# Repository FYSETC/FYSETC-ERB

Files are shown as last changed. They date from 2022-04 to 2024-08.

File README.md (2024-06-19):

# Introduction
ERB is a 3D printer multi-color control board based on RP2040, mainly used in Enraged Rabbit project. It can also be used in other two-axis stepper motor control situations.

# Update:
## [V1](./V1.0):
- MCU RP2040 
- 28V Input Max，5V@3A
- USB interface
- 2 x TMC2209 Onboard
- 5V RGB，Servo supported
- Extra pins are brought out to pin headers.

## [V2](./V2.0):
- Add CANBUS interface 
- Add 20*30 heat sinks 
- Replace with a 4Pin connector, which can be quickly plugged in and out, for Power & USB/CAN.
- Add optional USB and CANBUS interfaces 
- Add status indicator for Katapult bootloader or status indication.
- Preset thermistor temperature measurement circuit
- 12 x IO for gate sensors/switch
- Onboard integrated heat sink

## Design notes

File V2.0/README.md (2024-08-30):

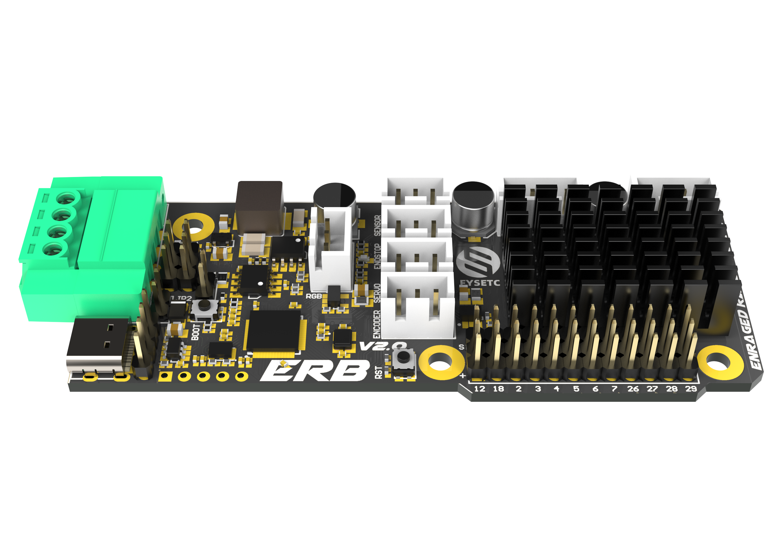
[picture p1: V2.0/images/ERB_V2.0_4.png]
erb


# Introduction

ERB V2 is a 3D printer multi-color control board based on RP2040, mainly used in Enraged Rabbit project. Based on V1, CANBUS connection is added, and the terminal connection method and layout are readjusted to better meet the needs of Enraged Rabbit V2.

## Features

- MCU RP2040 
- 28V Input Max，5V@3A
- USB & CANBUS interface
- 2 x TMC2209 Onboard
- 12 x IO for gate sensors/switch
- Onboard integrated heat sink
- 5V RGB，Servo supported
- Power supply/CAN integrated interface for easy connection

## Hardware

There are schemetic, silk and dwg file in `Hardware` folder.

### Pinout
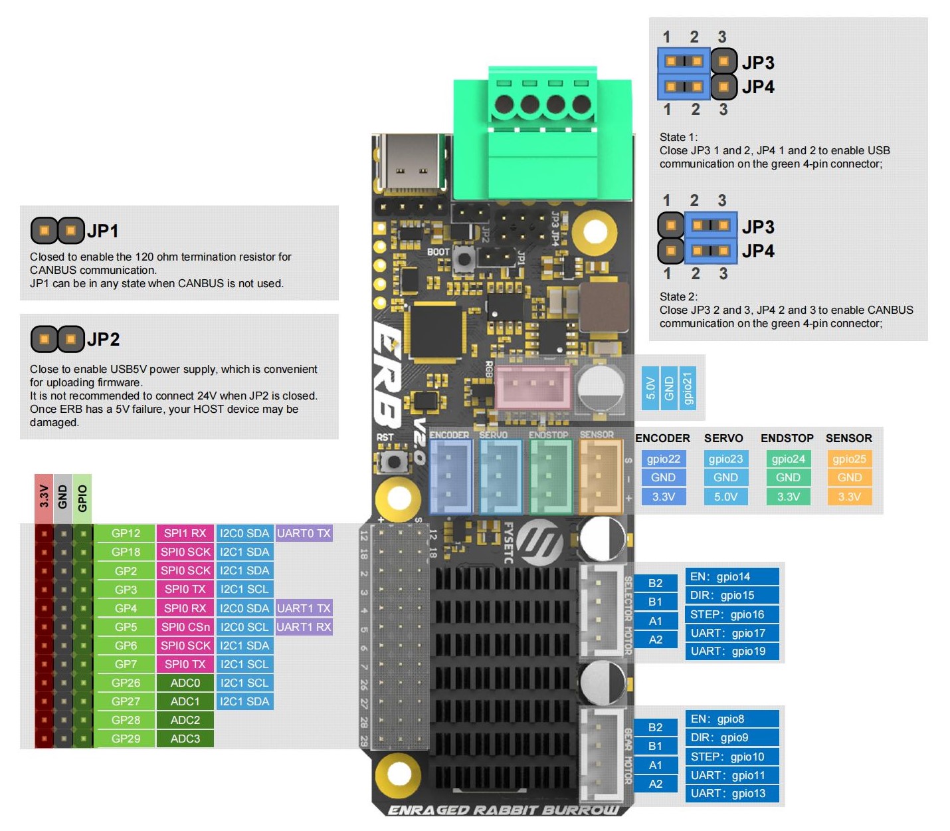
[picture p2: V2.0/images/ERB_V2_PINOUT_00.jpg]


## Firmware

### Compile and upload
In order to compile and upload at one time, you need to follow the steps below to put RP2040 into dfu mode.

1. Step 1: Connect 24V (Power on the board)
2. Step 2: Connect USB-C cable to your Klipper device (usually Raspberry Pi)
3. Step 3: Push and hold the BOOTSEL button
4. Step 4: Push the RST button and hold 0.5 seconds
5. Step 5: Release the RST button, after 3 seconds, Release the bootsel button
6. Verify your device is in boot mode connected by running the following command:

```shell
lsusb
```

The output should contain an entry looking like 2e8a:0003 Raspberry Pi RP2 Boot


On your klipper device (usually Raspberry Pi) run the following to create your make configuration:

```shell
cd  ~/klipper
make clean
make menuconfig
```

Select the following menuconfig settings

Use USB communication

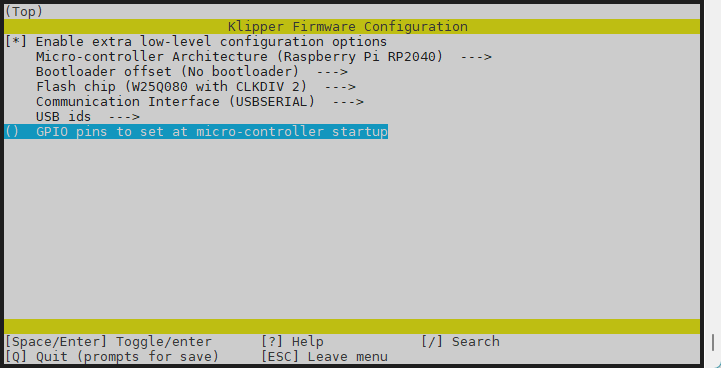
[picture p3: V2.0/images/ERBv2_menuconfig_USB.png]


Use CANBUS communication

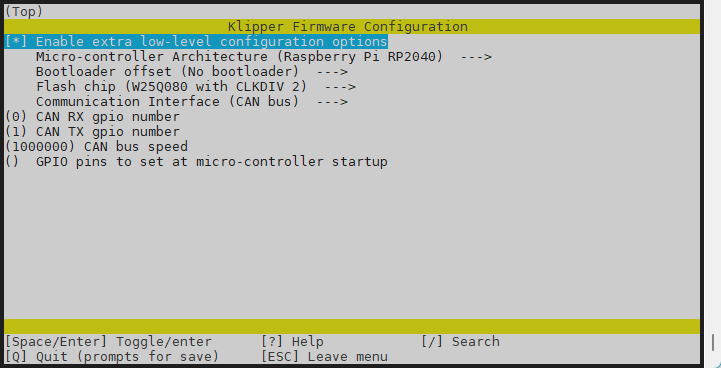
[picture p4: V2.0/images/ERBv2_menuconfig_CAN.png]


And create and upload the firmware files by running the following:

```shell
make flash FLASH_DEVICE=2e8a:0003
```
The output looks like the following - IF you are prompted (you might or might not) for a password, enter the password of your current user account.


Now restart your fystec-erb by disconnecting 24V - waiting some seconds and reconnecting 24V again.
Or press the reset button for one second and then release it.
You should be able to see it as usual klipper device within 
```shell
ls /dev/serial/by-id
```
### Configuration

See `ercf_hardware.cfg` in this repository `config` folder.

---------------------------------------------------

> [!TIP]
> We recommend using the katakulpt bootloader, whether you use USB or CANBUS communication. This can avoid many strange problems.
> 
> Configuration of the katakulpt bootloader:
> 
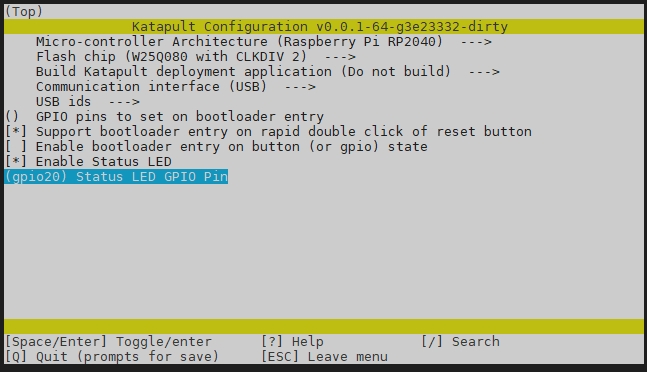
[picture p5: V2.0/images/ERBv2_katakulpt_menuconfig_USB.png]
ERBv2_katakulpt_menuconfig_USB
> 
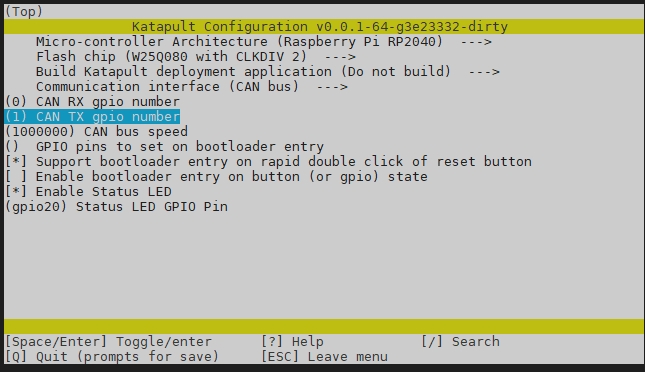
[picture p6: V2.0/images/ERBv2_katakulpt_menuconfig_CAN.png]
ERBv2_katakulpt_menuconfig_CAN
> 
> 
> Configuration of klipper using katakulpt:
> 
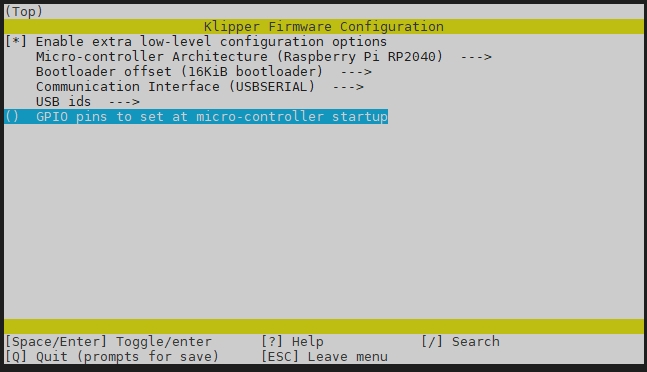
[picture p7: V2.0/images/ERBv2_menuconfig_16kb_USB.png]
ERBv2_menuconfig_16kb_USB
> 
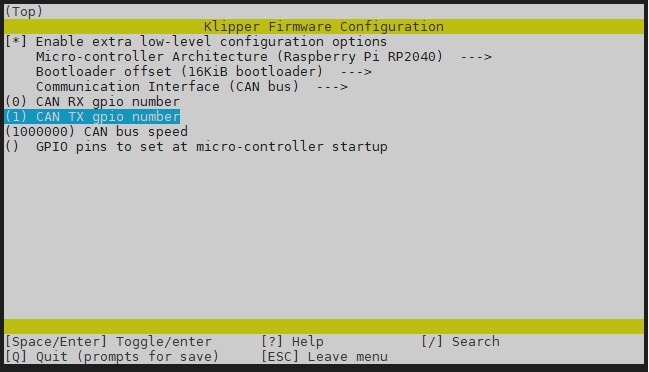
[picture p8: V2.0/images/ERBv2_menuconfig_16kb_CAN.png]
ERBv2_menuconfig_16kb_CAN
>

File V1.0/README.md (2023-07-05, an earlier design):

# FYSETC-ERB

This is dedicated controller board for VORON ERCF

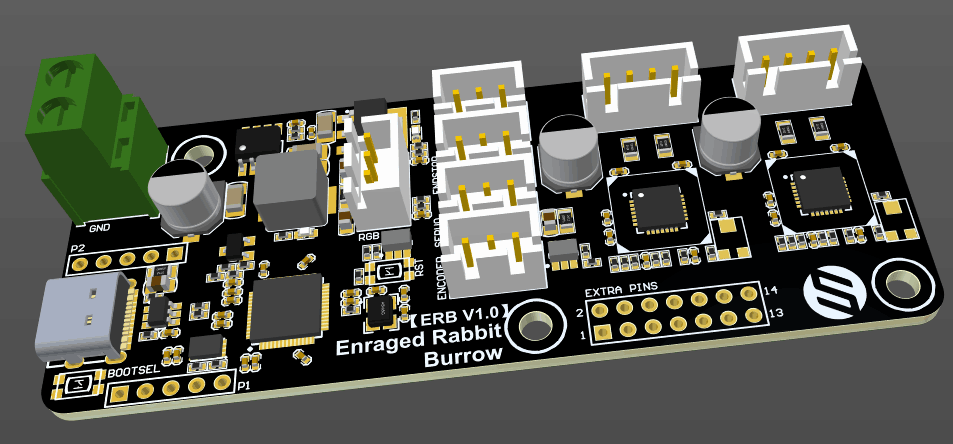
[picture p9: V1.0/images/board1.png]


## Features

1. Base on popular RP2040 chip, cheep,available

2. Power management chip, comparing to LDO chip, less heat, more powerful, more steady

3. USB type-C interface and more extra pins out.

## Hardware

There are schemetic, silk and dwg file in `Hardware` folder.

## Firmware

### Compile options
On your klipper device (usually Raspberry Pi) run the following to create your make configuration:

```shell
cd  ~/klipper
make clean
make menuconfig
```

Select the following menuconfig settings

makemenuconfig

And create the firmware files by running the following:

```shell
make
```

### Firmware upload

#### 1.With your windows PC

Step 1: Connect 24V (Power on the board)

Step 2: Connect USB-C cable to your Klipper device (usually Raspberry Pi)

Step 3: Push and hold the BOOTSEL button

Step 4: Push the RST button and hold 0.5 seconds

Step 5: Release the RST button, after 3 seconds, Release the bootsel button

Step 6: `RPI-RP2` folder will show up on your computer, copy your built firmware `klipper.uf2` to the folder.

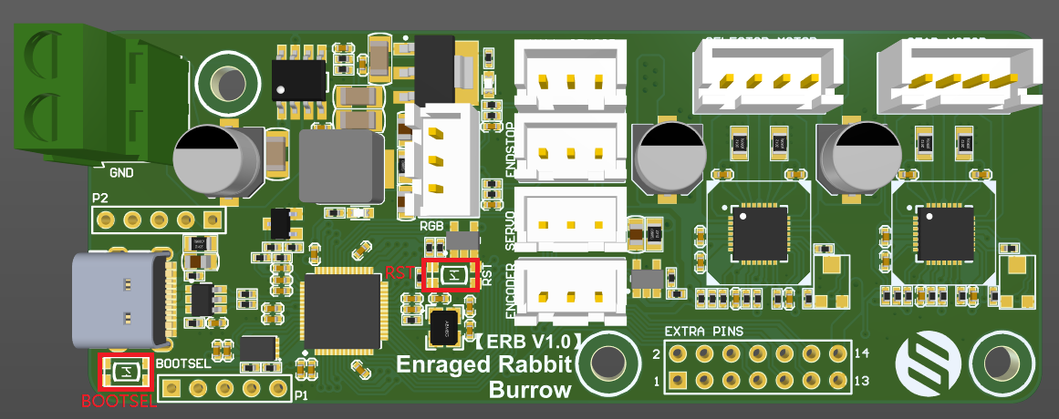
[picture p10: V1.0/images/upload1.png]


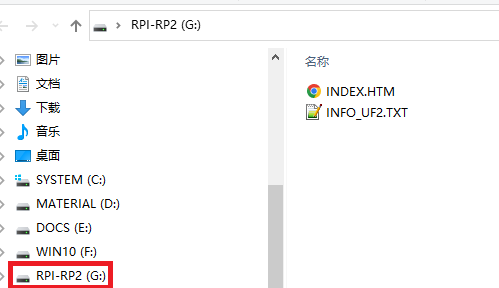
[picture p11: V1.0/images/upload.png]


#### 2. With your Pi 

Thanks for mk-maddin's work:
https://github.com/FYSETC/FYSETC-ERB/issues/2#issuecomment-1618902635

##### Connecting the board and bring it into flash mode

Step 1: Connect 24V (Power on the board)

Step 2: Connect USB-C cable to your Klipper device (usually Raspberry Pi)

Step 3: Push and hold the BOOTSEL button

Step 4: Push the RST button and hold 0.5 seconds

Step 5: Release the RST button, after 3 seconds, Release the bootsel button

Verify your device is in boot mode connected by running the following command:

```shell
lsusb
```

The output should contain an entry looking like 2e8a:0003 Raspberry Pi RP2 Boot


##### Flashing the firmware
Now we do not flash the fimware by directly copying it to the storage, but we flash it using the following command:

```shell
make flash FLASH_DEVICE=2e8a:0003
```

The output looks like the following - IF you are prompted (you might or might not) for a password, enter the password of your current user account.


Now restart your fystec-erb by disconnecting 24V - waiting some seconds and reconnecting 24V again.
You should be able to see it as usual klipper device within 
```shell
ls /dev/serial/by-id
```

### Configuration

See `ercf_hardware.cfg` in this repository `config` folder.

### Known issues

The mark of GPIO24 and GPIO25 is swapped, check the silk file [here](https://github.com/FYSETC/FYSETC-ERB/blob/main/hardware/Silk%20Fixed.pdf).

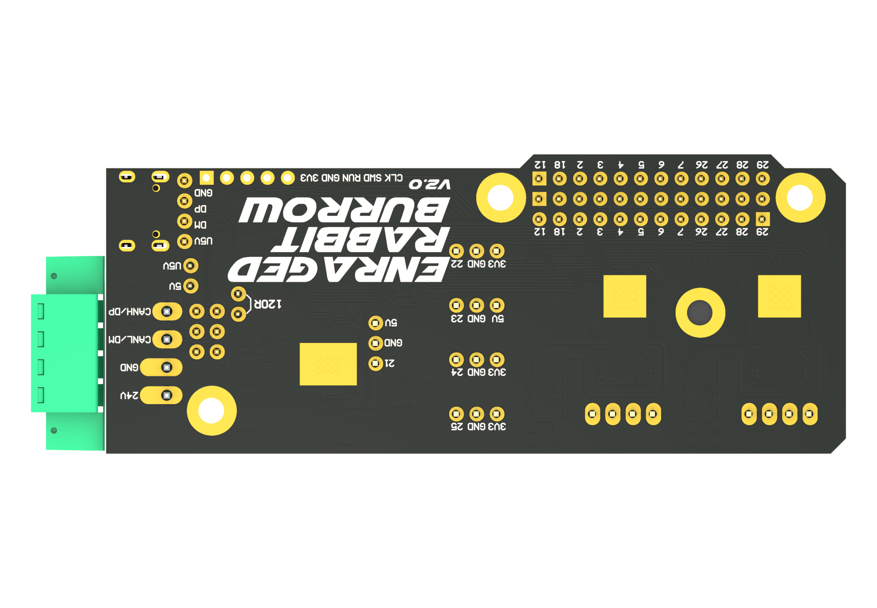
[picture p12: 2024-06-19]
V2.0/images/ERB_V2.0_2.png

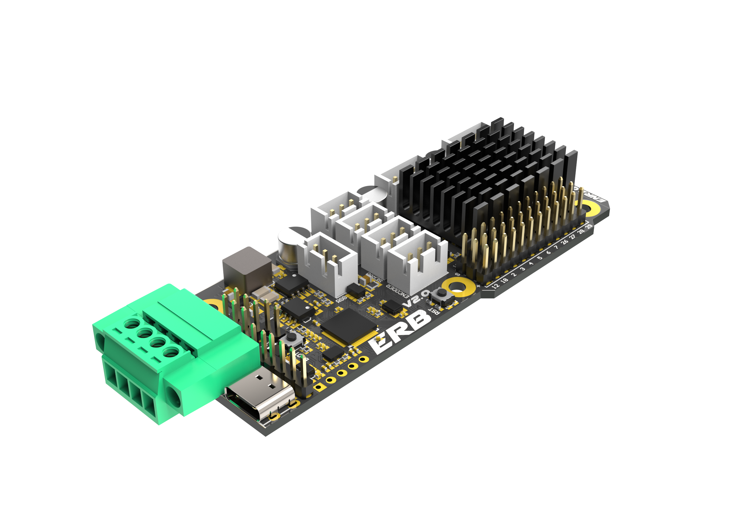
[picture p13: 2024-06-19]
V2.0/images/ERB_V2.0_3.png

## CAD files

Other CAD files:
V2.0/CAD/ERB V2.0.DWG

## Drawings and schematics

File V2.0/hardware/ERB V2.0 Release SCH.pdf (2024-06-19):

## Raspberry Pi

# GPIO4 6 GND 57

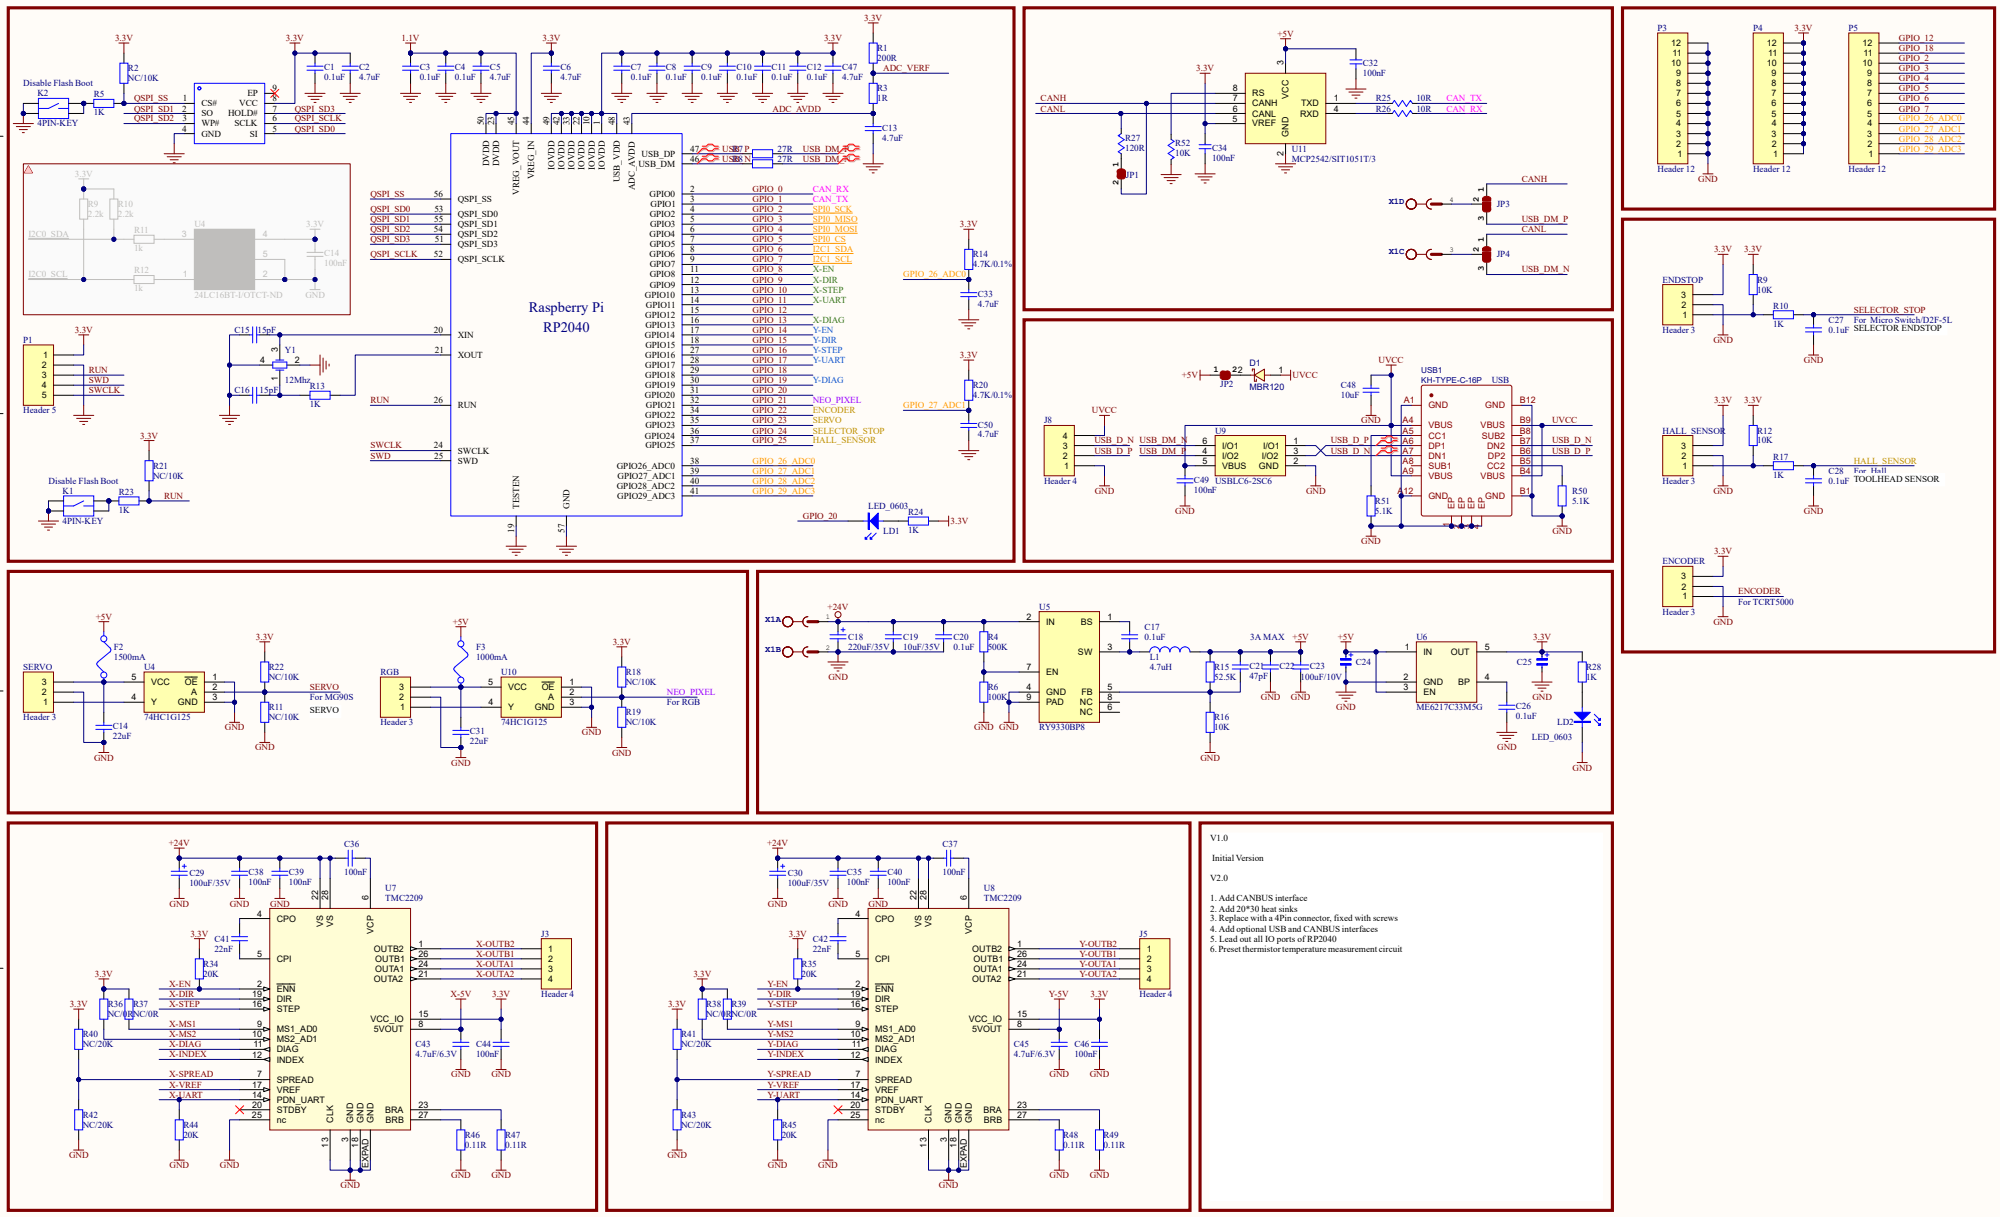
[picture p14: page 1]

1. Add CANBUS interface
2. Add 20*30 heat sinks
3. Replace with a 4Pin connector, fixed with screws
4. Add optional USB and CANBUS interfaces
5. Lead out all IO ports of RP2040
6. Preset thermistor temperature measurement circuit

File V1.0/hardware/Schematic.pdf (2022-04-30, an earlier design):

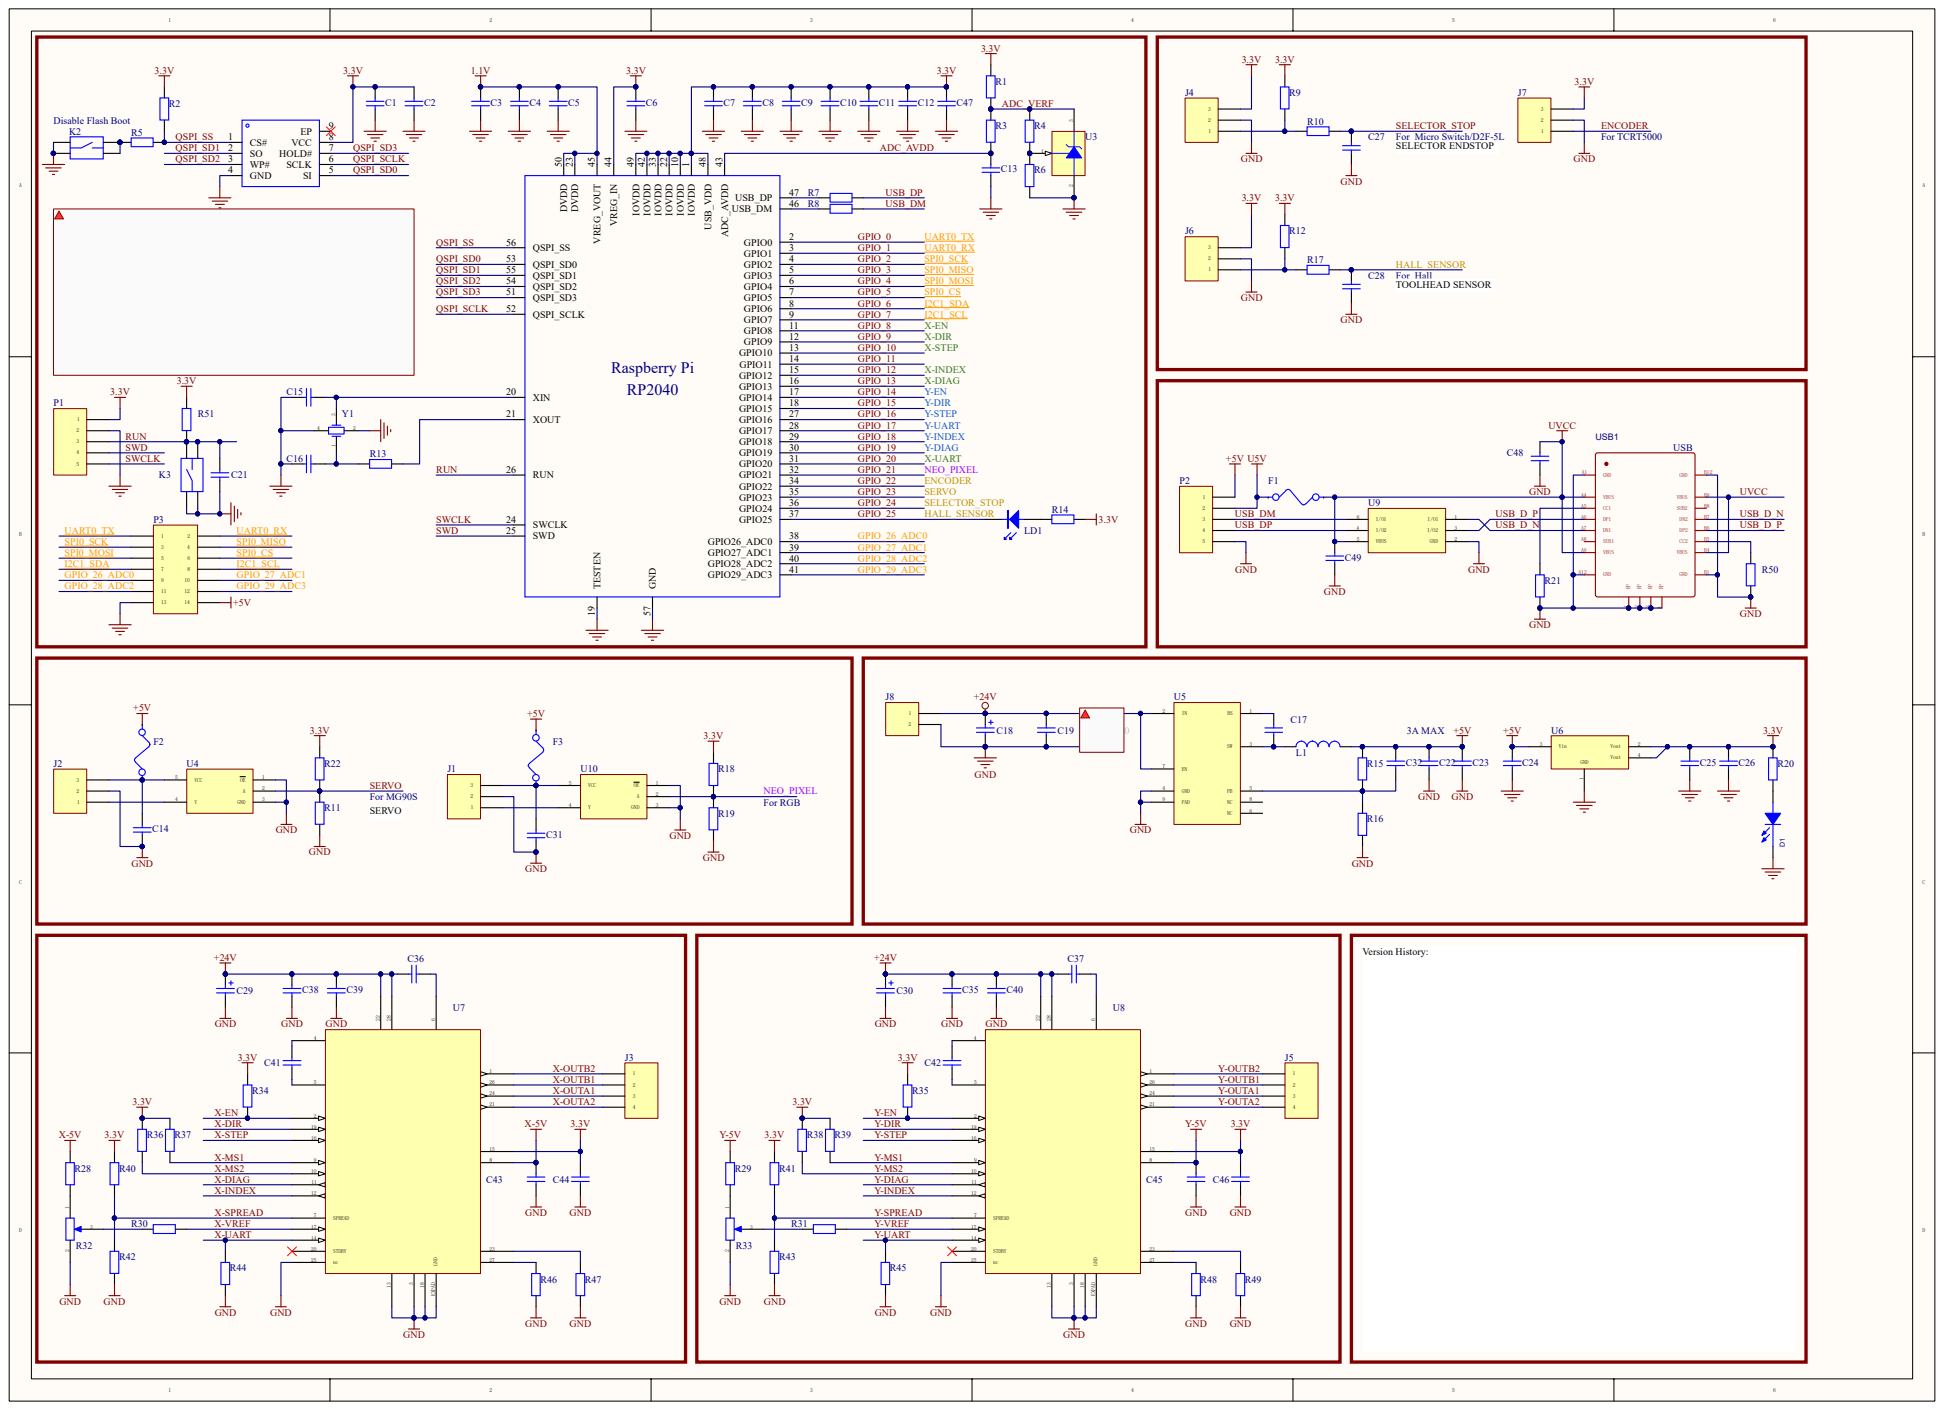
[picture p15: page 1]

XIN 20 | GPIO_7 I2C1_SCL GPIO_8 X-EN X-DIR X-STEP X-INDEX X-DIAG Y-EN Y-DIR Y-STEP Y-UART Y-INDEX Y-DIAG X-UART NEO_PIXEL ENCODER SERVO SELECTOR_STOP | GND

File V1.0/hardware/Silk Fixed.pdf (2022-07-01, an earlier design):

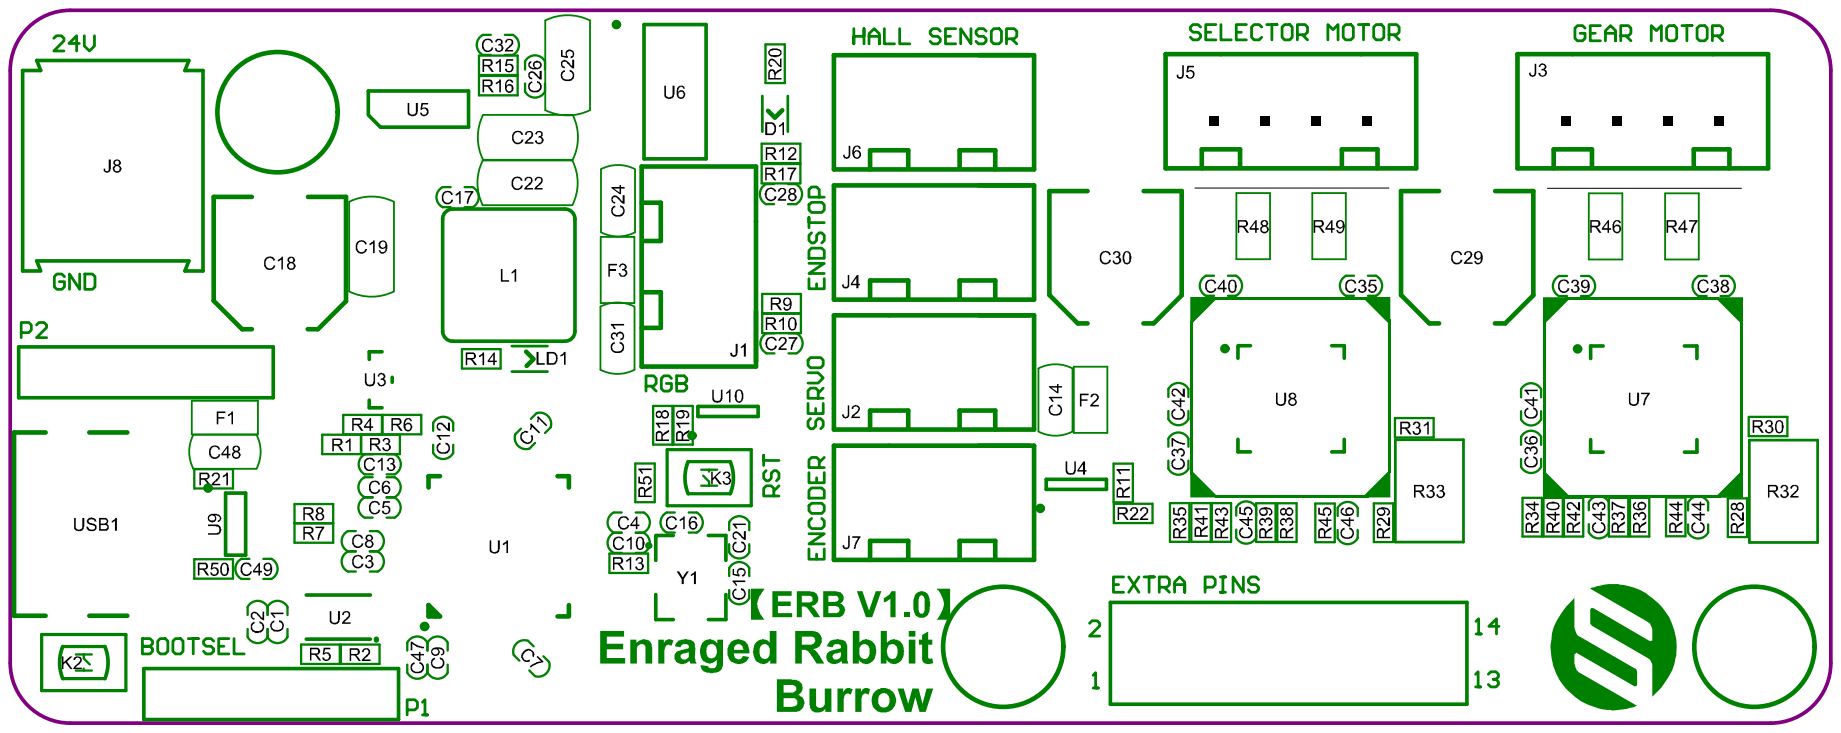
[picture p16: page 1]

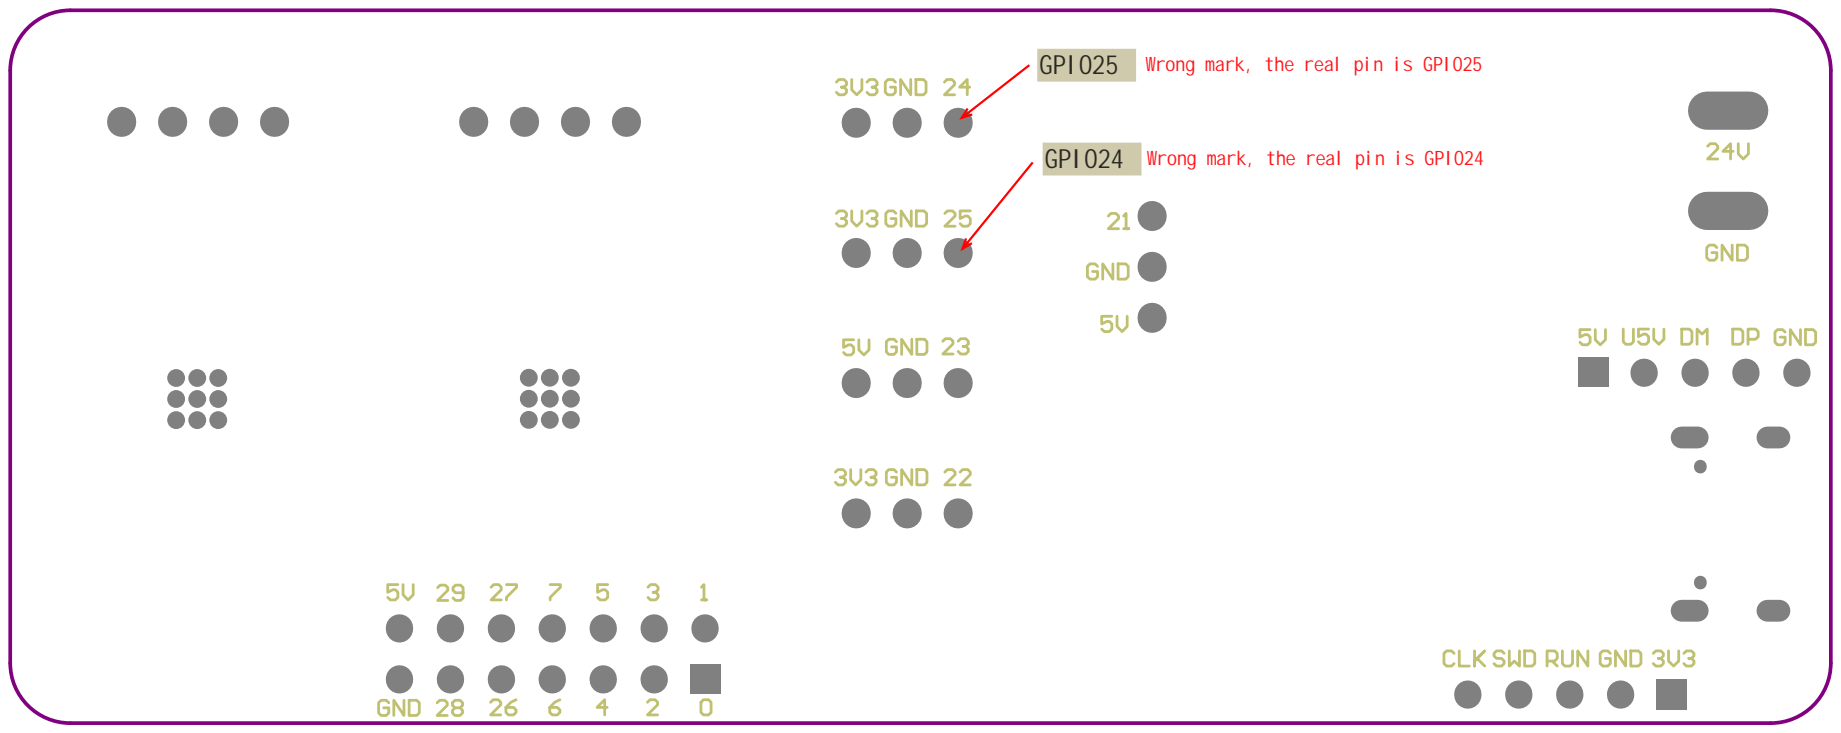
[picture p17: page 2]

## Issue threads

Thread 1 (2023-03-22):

Erb V1.1 make menuconfig

reneprettentaler, 2023-03-22:
Make menuconfig is not the same as in the reader.
What should I config in the menuconfig for flashing.
board does phenyl connct to Klipper with pressing the reset button.

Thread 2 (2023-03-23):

RP2040 MCU does not connect until reset is pressed

JoaquinBerrios, 2023-03-23:
The ERB board fails to connect to the host at boot until the reset button is pressed and the klipper service is re-started. This appears to be the same issue mentioned in the BTT SKR-Pico issue named here: https://github.com/bigtreetech/SKR-Pico/issues/2

I was able to implement a similar workaround as that mentioned in the thread and described in more detail here:
https://github.com/Drachenkaetzchen/VoronMisc/blob/main/SKR-Pico-Reset.md
by connecting pin 3 in P1 to a GPIO pin on my the host raspberry pi and resetting the ERB at boot time before the klipper service starts, but would prefer an actual fix that would allow me to undo that hack.

matthewj301, 2023-03-25:
yup also having this issue, although intermitently

JoaquinBerrios, 2023-05-03:
Looks like this was addressed in a commit last week in Klipper. I built firmware for a couple of RP2040 boards using the fixed usbserial.c from this commit and they connect via USB with no issues so far. Just thought I would share for other having this issue to try and see if this resolves it for them.
https://github.com/Klipper3d/klipper/commit/bec1d957d216986da8da216aca557c4d31623fd2

PatrikTheDev, 2023-05-20:
I’m running the latest Klipper version (both ERB and Pi) and I’m still having issues, though mine doesn’t connect after a reset, it often needs MUCH more convincing. I already requested a partial refund but is there a way to save the board? That Klipper commit didn’t work for me since I’m running it already

mk-maddin, 2023-06-16:
@PatrikTheDev
I was able to resolve this issue by flashing with the following options - Klipper v0.11.0-221-g6ce2bd61

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

PatrikTheDev, 2023-06-16:
IIRC that’s what I flashed with before but it didn’t work. I got it working with the CanBoot workaround though. As it turns out the board still wasn’t quite healthy and I got a partial refund from Fysetc

mk-maddin, 2023-06-16:
ok...maybe I was a bit too fast - I am now running into "Timeout on wait for 'tmcuart_response' response" error on like every seconds stepper_buzz command
Re-flashing with the default chip "W25Q080 with CLKDIV 2" solves the stepper_buzz error, but again causes disconnect at every restart

PatrikTheDev, 2023-06-16:
Have you tried flashing CanBoot to it yet? Seems to also work for the SKR Pico

mk-maddin, 2023-06-17:
No not yet ...
I am not using CanBus at all at the moment and after reading through the CanBoot guideline, to be truth I have no idea how to "2. Build klipper wiht CAN support" ( https://github.com/Arksine/CanBoot#uploading-klipper )

PatrikTheDev, 2023-06-17:
I’m not using CAN either right now, CanBoot offers a USB mode. Look into the SKR Pico repo, issue number 2 for more information

mk-maddin, 2023-06-17:
To be truth I am not 100% sure if I really see the same issue as the skr pico people describe ...
My device does not show at all within /dev/serial/* or /dev/tty* after every RST or power disconnect of 24V,
until I re-flash a .uf2 via the "storage" (pressing "bootsel"+"rst")  mode.
I can press "rst" during boot or run the [GPIO workaround](https://github.com/Drachenkaetzchen/VoronMisc/blob/main/SKR-Pico-Reset.md) - all without any success unti I re-flash and keep the device online.

So klipper not able being to connect is only a "victim" of the ERB not correctly booting into the flashed firmware / serial mode after power off / reset.
This happens as I just tested for klipper.uf2 as for canboot.uf2

jeanres, 2023-06-28:
Same issue here.

mk-maddin, 2023-07-03:
I think I was able to solve the issue for me now by using the same flash procedure as done with the 3D Mellow Fly ERCF Easy BRD board ( https://mellow.klipper.cn/#/board/fly_ercf/flash ) - as most of this is chinese and I had to translate via online translator service - here is what I did:

### **1. Prepare Firmware**
On your klipper device (usually Raspberry Pi) run the following to create your make configuration:
`cd  ~/klipper`
`make clean`
`make menuconfig`

Select the following menuconfig settings
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
And create the firmware files by running the following:
`make`

### **2. Connecting the board and bring it into flash mode**
Step 1: Connect 24V (Power on the board)
Step 2: Connect USB-C cable to your **klipper device** (usually Raspberry Pi)
Step 3: Push an hold `BOOTSEL` button
Step 4: Click `RST` button
Step 5: Release `RST` and `BOOTSEL` button at the same time

Verify your device is in boot mode connected by running the following command:
`lsusb`

The output should contain an entry looking like `2e8a:0003 Raspberry Pi RP2 Boot`
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

### **3. Flashing the firmware**
Now we do not flash the fimware by directly copying it to the storage, but we flash it using the following command:
`make flash FLASH_DEVICE=2e8a:0003`
The output looks like the following - IF you are prompted (you might or might not) for a password, enter the password of your current user account.
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

Now restart your fystec-erb by disconnecting 24V - waiting some seconds and reconnecting 24V again.
You should be able to see it as usual klipper device within /dev/serial/by-id

Hope this helps :)

Erfa1l, 2023-07-09:
Got the same issue on Klipper v0.11.0-240-g6d48adf9, Everytime when printer reboots I need to manualy disconnect usb -> press RST for a couple of second -> plug USB in. Only this steps help raspberry pi 4 to recognize device.. The hack from 1st post is now working for me :(

Mapiiik, 2023-08-03:
We have also problems with ERB v1.1 board. With `Flash chip (W25Q080 with CLKDIV 2)` board boot only after imediate flash and reboot. After power off/on we can't achieve USB connection even if we tried with pressing RST/disconnectig/connecting.

With `Flash chip (GENERIC_03H with CLKDIV 4)` board boots OK every time, but is unusable, if we send any commands to it, it almost every time stops with
`Timeout on wait for 'tmcuart_response' response`

Has anyone managed to solve these problems?

ammoniak, 2023-11-03:
Same thing here, it works after flashing but not after restarting/connecting it again, etc.

tdlane1, 2023-11-27:
Encountering the same issue as Mapiik [here](https://github.com/FYSETC/FYSETC-ERB/issues/2#issuecomment-1664349622), running Klipper v0.12.0-9

jamseywood, 2024-01-30:
I am having the same issue, is there any update?

ngandalf, 2024-02-03:
I am having the same issue with latest version of klipper :-( the workaround of JoaquinBerrios  dosn't work for me i need to flash the erb board to detect the device with klipper

salocain, 2024-02-04:
same issue , work well before, but....after  5v servo port dead, now.... connecting problem..... it's not a good product ....

fysetc do a commercial offer ?

jamseywood, 2024-02-04:
so I have done some digging and it looks like the Pi chip is at fault here. There was a bug that caused the RP chip to not detect USB connections on boot randomly. Unfortunatly it looks like there is not real fix for this as we cannot change the low level code on the chip. There are hardware 'hacks' that require soldering a wire from the reset switch to an addressable pin where you can call a function to reset the board as needed, but not an ideal solution. I have moved over to the standard ERCF board and its been faultless, only issue being that every prin was backward, but easy enough to fix.

salocain, 2024-02-04:
> so I have done some digging and it looks like the Pi chip is at fault here. There was a bug that caused the RP chip to not detect USB connections on boot randomly. Unfortunatly it looks like there is not real fix for this as we cannot change the low level code on the chip. There are hardware 'hacks' that require soldering a wire from the reset switch to an addressable pin where you can call a function to reset the board as needed, but not an ideal solution. I have moved over to the standard ERCF board and its been faultless, only issue being that every prin was backward, but easy enough to fix.

can you give me a link for this hack explaination?

thank you

jamseywood, 2024-02-04:
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

https://github.com/matthew-humphrey/3DP-Build-Log/blob/main/RP2040-USB-Bug/README.md

JoaquinBerrios, 2024-02-04:
> so I have done some digging and it looks like the Pi chip is at fault here. There was a bug that caused the RP chip to not detect USB connections on boot randomly. Unfortunatly it looks like there is not real fix for this as we cannot change the low level code on the chip. There are hardware 'hacks' that require soldering a wire from the reset switch to an addressable pin where you can call a function to reset the board as needed, but not an ideal solution. I have moved over to the standard ERCF board and its been faultless, only issue being that every prin was backward, but easy enough to fix.

I explain what pin to connect to in my post above from March 23. No need to solder anything and can be implemented by connecting the pin on the board to a free GPIO pin on the pi/host computer. The pin I reference in my post is the reset pin you need to connect to and is already routed to the header on this board. If you don't want to toggle with with a GPIO pin, you can also connect a manual switch that will short the pin to ground to reset manually, although that is more of a pain than automating the reset.

Also, the core issue with the RP2040 was addressed in a Klipper update some time back (see my post above on May 2). My board is still working fine for me running the current version of Klipper on my MCU so I wouldn't think it's regression of the issue. If you haven't flashed your board to the current version of Klipper, try that before hacking around with workarounds. You can check the version of Klipper on your MCUs in the "System" menu in Fluidd. I'm sure Mainsail has a similar screen where you can check the version of the firmware on your MCUs. If it's older than the commit I reference above, you will need to flash your board with the current version of Klipper.

This shouldn't make a difference, but I also flashed CanBoot/Katapult on my board since I have the board connected via CANbus. If you update to the current version of Klipper and your board still has the issue, try flashing Katapult, re-flashing Klipper and see if that helps. You can still connect the board via USB even if you flash it with Katapult, just build Klipper to connect via USB instead of CAN.

If all this doesn't work and you are considering a new board, take a look at the BTT MMU. It's bult on an STM controller, replaceable stepper drivers, and a ton of other features to better support the ERCF v2.

tokamac, 2024-09-11:
Solution is here:
https://github.com/FYSETC/FYSETC-PortableInputShaper/issues/8#issuecomment-1661327659

BreeOge, 2024-12-07:
> Solution is here: [FYSETC/FYSETC-PortableInputShaper#8 (comment)](https://github.com/FYSETC/FYSETC-PortableInputShaper/issues/8#issuecomment-1546991452)

Does not work.  its just a POS!

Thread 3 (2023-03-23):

Menuconfig options missing from documentation

JoaquinBerrios, 2023-03-23:
The current documentation for building the klipper firmware for the MCU on this board does not indicate values for the build options available in the current version of klipper. Could you please update the documentation to specify the values needed to build a current version?

Currently, make menuconfig prompts for the following values when RP2040 is selected as the micro-controller architecture:

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

matthewj301, 2023-03-24:
Same issue here

matthewj301, 2023-03-24:
Just a follow up, I just ended up trying a few options, and what seemed to work for me was:
[*] Enable extra low-level configuration options
    Micro-controller Architecture (Raspberry Pi RP2040)  --->
    Bootloader offset (No bootloader)  --->
    Flash chip (W25Q080 with CLKDIV 2)  --->
    Communication interface (USB)  --->
    USB ids  --->
()  GPIO pins to set at micro-controller startup (NEW)

Haven't actually tried using it yet, but Klipper (RatOS) now recognizes it (using https://github.com/moggieuk/ERCF-Software-V3). You'll still have to connect it to a PC initially and copy over the binary to the ERB

JoaquinBerrios, 2023-03-25:
Just to confirm that I have done builds with the options set to what I posted above and they have worked fine. At least I was able to get through all the testing and calibration steps.  I settled on the flash chip after looking at the components on the board, so it would be nice if the officially recommended options were included in the documentation to save future users some grief either worrying that they are going to brick their board or having to look up components on the boards to figure out how to build.

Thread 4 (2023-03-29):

Doesn't stay up

Oasis1981, 2023-03-29:
The blue light powered on with the combo button, but when i release the rst button goes off.

and i can't connect on it

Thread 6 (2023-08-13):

selector endstop pin is reversed in fysetc 's hardware config file

ntchris, 2023-08-13:
selector endstop pin is reversed in fysetc 's hardware config file

selector endstop pin is defined reversed in fysetc 's hardware config file with the wrong ! symbol

**wrong (current version of file)**
`# Select the endstop you want depending if you are using sensorless homing for the selector or not
endstop_pin: !ercf:gpio24    # has ! , but shouldn't
`

`
According to klipper doc,    https://www.klipper3d.org/Config_Reference.html
Pin names may be preceded by ! to indicate that a reverse polarity should be used (eg, trigger on low instead of high).
`
since it's normally closed, it's pull down to GND, so it's normally LOW, with a ! ,   so it's normally triggered.
wrong behaviour:
when micro switch is not pressed, it's "triggered" from the command query_endstops.

**correct:**
endstop_pin: ercf:gpio24   # remove the !
when micro switch is not pressed ( normally close) , it's "open" in command result
query_endstops
manual_stepper gear_stepper:open manual_stepper selector_stepper:open x:open y:open z:open

when micro switch is pressed ( open) , it's "triggered" in command result
`manual_stepper gear_stepper:open manual_stepper selector_stepper:TRIGGERED x:open y:open z:open`

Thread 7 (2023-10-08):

Documentation required: pin headers (P1, P2)

k1-801, 2023-10-08:
The pin headers P1 and P2 and their uses are not documented. It seems like P2 is meant for jumpers, like the pin header on EasyBoard, but it is never explicitly stated anywhere on the repository. It might be a good idea to put this info somewhere (readme.md ?)

the-muldoon, 2023-11-26:
Did you happen to ever find out how to fix this issue?
In the ercf_softwarecfg, the documentation says:
[ercf]
encoder_pin = ^P1.0
encoder_resolution = 1.365188

But I get an error message of:
Pin 'P1.0' is not a valid pin name on mcu 'mcu'

k1-801, 2023-11-26:
> But I get an error message of: Pin 'P1.0' is not a valid pin name on mcu 'mcu'

Couldn't solve it either, had to switch to tge Happy Hare config instead, but it also gives errors, but different - but at least the author actually responded and promised to solve it.

the-muldoon, 2023-11-27:
Thanks for the quick response! I've been pulling my hair out for days on it. I was getting ready to try Happy-Hare anyway! Hopefully, this link will help others in the future.
https://github.com/moggieuk/Happy-Hare

eliwong, 2023-12-04:
> The pin headers P1 and P2 and their uses are not documented. It seems like P2 is meant for jumpers, like the pin header on EasyBoard, but it is never explicitly stated anywhere on the repository. It might be a good idea to put this info somewhere (readme.md ?)

You should be able to see each pin information for P1 and P2 on the back of the board.

P2 is used for backup USB connections. Some people think USB-C may be unstable or can be used when space does not allow.
At the same time, by connecting U5V and 5V through a jumper cap, the board can be temporarily powered through USB, and there is no need to connect to 24V when burning firmware.

P1 is the SWD debugging interface of RP2040. In most cases, it cannot be used unless you are a developer and need to debug code.

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

eliwong, 2023-12-04:
> Did you happen to ever find out how to fix this issue? In the ercf_softwarecfg, the documentation says: [ercf] encoder_pin = ^P1.0 encoder_resolution = 1.365188
>
> But I get an error message of: Pin 'P1.0' is not a valid pin name on mcu 'mcu'

Are you talking about klipper's configuration?
When using the RP2040 control board, the pin configuration should be written as gpio**, such as ERB's encoder pin: gpio22

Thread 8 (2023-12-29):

What is P1.27?

thisiscam, 2023-12-29:
Hi,

I wonder why the config says
```
#diag_pin: ^P1.27      # Set to MCU pin connected to TMC DIAG pin
```

https://github.com/FYSETC/FYSETC-ERB/blob/main/config/ercf_hardware.cfg#L47

The X_DIAG appears to be connected to `ercf:gpio13` so shouldn't this be:
```
#diag_pin: ecrf:gpio13
```
?

slightlysketch, 2024-04-10:
It’s pin gpio19
If youre using the board for an ERCF it’s
ERCF:gpio19

granted if you swap the motor and selector motors around and change the pin sets for everything and sort out the confit you can end up using the sensorless homing for the tool head sensor which eliminates an issue with using random tool heads that aren’t made for this, as getting a sensor and a bad hall sensor at that, into small spaces is a nightmare and I couldn’t for the life of me figure out how to disable using a tool head sensor without breaking other macros.

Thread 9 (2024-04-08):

Timer too close with "gear" motor (v1.1 ERB)

warpwookie, 2024-04-08:
Hello I'm not sure what to do but I'm getting a timer too close error and my printer stops. This is only when trying to activate the "Gear" motor. the selector motor works fine, and when I connect the "gear" stepper into the "selector" port it runs as well. even with no cable connected when I try to test the "gear" motor it stops my printer and give Timer too close with mcu "mmu". It seems to be the port, I'm not sure what to do, please help! I also cannot find a pinout diagram or any documentation on the V1.1 board, very upsetting because it is being sold on the market with no information, shame.

slightlysketch, 2024-04-10:
I can help.
At work now.

Spent all night with this board and even got sensorless tool head sensor working with it.

Please post your klippy logs and your config files.

slightlysketch, 2024-04-10:
also before I even check all that, what is your host for pi? Are you using the cable they sent? It’s trash and don’t use it. Buy a quality cable as crap cable can cause that error.

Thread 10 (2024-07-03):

Max 5V Current Draw on V2

zhou13, 2024-07-03:
What is the max Max 5V Current Draw on V2.0?

It says that "28V Input Max，5V@3A" however this is not clear to me whether this is the5V@3A is input or output. I'd like to build https://github.com/kevinakasam/ERCF_Filament_Cutter and I need to decided whether I need a dedicated 5V power supply to power the servo.

MasterOfGamerino, 2024-09-15:
So the [schematics](https://github.com/FYSETC/FYSETC-ERB/blob/main/V2.0%2Fhardware%2FERB%20V2.0%20Release%20SCH.pdf) provide some clearer information on this:
The boards 5 V regulator has a max output of 3 A. This is shared for every component on the board, however, including the 3 V LDO.
The 5 V pin on the SERVO header is fused with 1500 mA, the one on the RGB header is fused with 1000 mA.

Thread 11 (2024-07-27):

What is the VREF of each stepper drivers?

JonasBouchard, 2024-07-27:
I am looking to use this board on something else than an ERCF and I would need to know the VREF of each stepper drivers.

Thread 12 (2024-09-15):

board flashing problem 1.1

borislavstefanov, 2024-09-15:
hello, for several days I have been trying to flash the board version 1.1 by following the steps but there is no response, it even shows me in ssh as an active device, I also tried with a connection to the PC but again it has no effect. I tried pressing the boot and reset button as it says, but it has no effect. please help

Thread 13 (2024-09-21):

PC based flashing instructions

Person1873, 2024-09-21:
When flashing the board from a PC, there is no need to connect 24v.

You can simply add a jumper between 5V & U5V.
this should be reflected in the instructions as this is quite common for MCU boards in the klipper ecosystem

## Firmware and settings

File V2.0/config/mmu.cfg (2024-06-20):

###########################################################################
# Happy Hare MMU hardware pin config
#
# EDIT THIS FILE BASED ON YOUR SETUP
#
# This contains aliases for pins for MCU type ERB
#
[mcu mmu]
# Change to `canbus_uuid: 1234567890` for CANbus setups
serial: /dev/serial/by-id/usb-Klipper_rp2040_E6612C771F26872B-if00 


# Section to create alias for pins used by MMU for easier integration into Klippain and RatOS.
# The names match those referenced in the mmu_hardware.cfg file. If you get into difficulty
# you can also comment out this aliases definition and configure the pin names directly
# into mmu_hardware.cfg.
#
[board_pins mmu]
mcu: mmu # Assuming using an external / extra mcu dedicated to MMU
aliases:
    MMU_GEAR_UART=gpio11,
    MMU_GEAR_STEP=gpio10,
    MMU_GEAR_DIR=gpio9,
    MMU_GEAR_ENABLE=gpio8,
    MMU_GEAR_DIAG=gpio13,
    MMU_SEL_UART=gpio17,
    MMU_SEL_STEP=gpio16,
    MMU_SEL_DIR=gpio15,
    MMU_SEL_ENABLE=gpio14,
    MMU_SEL_DIAG=gpio19,
    MMU_SEL_ENDSTOP=gpio24,
    MMU_SERVO=gpio23,
    MMU_ENCODER=gpio22,
    MMU_GATE_SENSOR=,
    MMU_NEOPIXEL=gpio21,
    MMU_PRE_GATE_0=gpio12,
    MMU_PRE_GATE_1=gpio18,
    MMU_PRE_GATE_2=gpio2,
    MMU_PRE_GATE_3=gpio3,
    MMU_PRE_GATE_4=gpio4,
    MMU_PRE_GATE_5=gpio5,
    MMU_PRE_GATE_6=gpio6,
    MMU_PRE_GATE_7=gpio7,
    MMU_PRE_GATE_8=gpio26,
    MMU_PRE_GATE_9=gpio27,
    MMU_PRE_GATE_10=gpio28,
    MMU_PRE_GATE_11=gpio29,
